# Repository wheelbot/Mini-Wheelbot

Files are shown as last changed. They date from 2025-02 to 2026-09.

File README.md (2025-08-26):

<!-- ![The Mini Wheelbot](imgs/intro.png) -->
<!-- ![Teaser](imgs/teaser.png) -->
<div align="center">
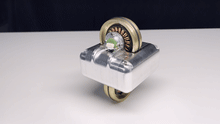
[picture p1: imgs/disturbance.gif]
  
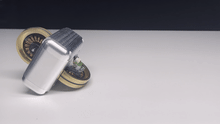
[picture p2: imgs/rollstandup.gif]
  
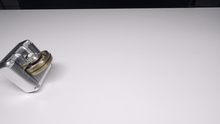
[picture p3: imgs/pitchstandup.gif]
  
</div>

<div align="center">
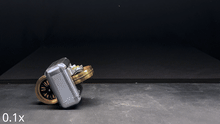
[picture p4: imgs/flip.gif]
  
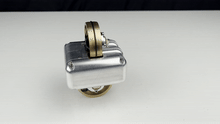
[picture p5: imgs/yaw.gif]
  
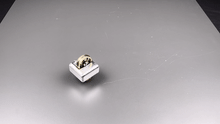
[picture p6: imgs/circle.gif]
  
</div>

# The Mini Wheelbot

The Mini Wheelbot is a **balancing, reaction wheel
unicycle robot** designed as a testbed for learning-based control.
It is an unstable system with highly nonlinear yaw dynamics, non-holonomic driving, and discrete contact switches in a small, powerful, and rugged form factor. 
The Mini Wheelbot can use its wheels to stand up from any initial orientation – enabling automatic environment resets in repetitive experiments.

## Videos
An overview of Wheelbot Hardware is available here:
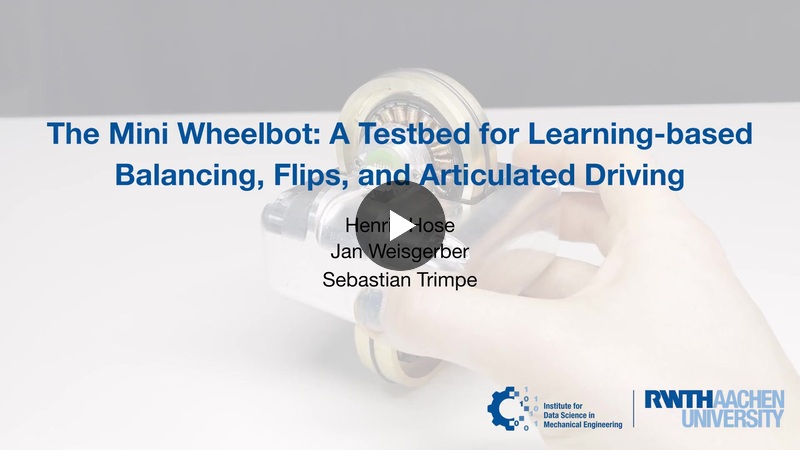
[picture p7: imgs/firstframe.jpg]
ICRA 2025 Video (https://youtu.be/_d7AqTRjz6g)


## Citation
The Mini Wheelbot is introduced in the paper:
[Henrik Hose, Jan Weisgerber, and Sebastian Trimpe. **"The Mini Wheelbot: A Testbed for Learning-based Balancing, Flips, and Articulated Driving"**, accepted to the IEEE International Conference on Robotics and Automation ICRA (2025).](http://arxiv.org/abs/2502.04582)

Please cite our paper on the Mini Wheelbot:
```bibtex
@inproceedings{hose2025miniwheelbot,
    title={The Mini Wheelbot: A Testbed for Learning-based Balancing, Flips, and Articulated Driving},
    author={Hose, Henrik and Weisgerber, Jan and Trimpe},
    year={2025},
    booktitle={2025 IEEE International Conference on Robotics and Automation (ICRA)}
}
```

## Papers using the Mini Wheelbot Hardware
The following papers use Mini Wheelbot:
- [Henrik Hose, Jan Weisgerber, and Sebastian Trimpe. **"The Mini Wheelbot: A Testbed for Learning-based Balancing, Flips, and Articulated Driving"**, accepted to the IEEE International Conference on Robotics and Automation ICRA (2025).](http://arxiv.org/abs/2502.04582)
- [Hose, Henrik, Paul Brunzema, Alexander von Rohr, Alexander Gräfe, Angela P. Schoellig, and Sebastian Trimpe. **"Fine-Tuning of Neural Network Approximate MPC without Retraining via Bayesian Optimization."** In CoRL Workshop on Safe and Robust Robot Learning for Operation in the Real World. 2024.](https://openreview.net/pdf?id=lSah6an1Ar)

## Structure of this Repo
This repo contains the following materials:
- [**PCB Schematics**](./hardware/electronics/schematic/): PCBs used on the Mini Wheelbot
- [**Meshes**](./hardware/meshes/): for visualization
- [**Wheelbot-Lib**](./wheelbot-lib/): C++20 code running on the Mini Wheelbots Buildroot Linux
- [**Scripts**](./wheelbot-lib/scripts/): Collection of Python Scripts used for system identification, keyboard control, etc.
- [**Simulation**](./simulation/): ODEs describing the Mini Wheelbot's dynamics in different Python and simulation in Acados.
- [**Microcontroller software**](./hardware/microcontroller-software/) running on STM32 microcontrollers on the Mini Wheelbot.

## Related Repos and Acknowledgements
Related repositories:
- [**Yaw control neural network approximate MPC**](https://github.com/hshose/mini-wheelbot-ampc): Dataset synthesis and neural network training in Jax for nonlinear yaw control on the Mini Wheelbot.

The Mini Wheelbot's development has been made possible thanks to these open-source projects:
- [**modm**](https://modm.io/): A modern C++ barebone embedded library generator
- [**KiCAD**](https://www.kicad.org/): A Cross Platform and Open Source Electronics Design Automation Suite
- [**CasADi**](https://web.casadi.org/): A symbolic framework for numeric optimization implementing automatic differentiation
- [**Buildroot**](https://buildroot.org/): A tool to generate embedded Linux systems through cross-compilation.
- [**acados**](https://github.com/acados/acados): Fast and embedded solvers for nonlinear optimal control.
- [**µMotor**](https://github.com/roboterclubaachen/micro-motor): A motor controller for BLDC and DC motors up to 250W.
- [**JAX**](https://jax.readthedocs.io.): Composable transformations of Python+NumPy programs.

## Contact
If you are interested in building your own Mini Wheelbot, [contact us](https://www.dsme.rwth-aachen.de/cms/dsme/das-institut/team/~ujxgg/henrik-hose/?lidx=1).

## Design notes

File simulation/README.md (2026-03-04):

# Intro
The "joints" of the wheelbot are in order:

1. The yaw angle $\psi$; its derivative is the yaw rate~$\dot{\psi}$.
2. The roll angle $\phi$; its derivative is the roll rate~$\dot{\phi}$.
3. The pitch angle $\theta$; its derivative is the pitch rate~$\dot{\phi}$.
4. The driving wheel angle $q_w$ that is actually doesn't appear in the equations of motions; its derivative is the wheel rotational velocity $\dot{q}_W$; the input torque applied to this joint is $\tau_W$.
5. The reaction wheel angle $q_w$ that is actually doesn't appear in the equations of motions; its derivative is the wheel rotational velocity $\dot{q}_R$; the input torque applied to this joint is $\tau_R$.

The generalized coordinates are: $q=[\psi,\phi,\theta,q_W, q_R]^\top$

The inputs of the wheelbot are: $u=[\tau_W, \tau_R]$

## Continuous time
In continuous time, the dynamics are of the form: $M(q)\ddot{q}+b(q,\dot{q})+g(q,u)=0$.
The mass matrix $M$, coriolis and centripedal terms $b$, and gravitational terms and inputs $g$ are also parametric in the mass and inertia of the wheels W and R, and the body of the robot, and in the wheel radius and distance from wheel rotational axis to body center of mass (assumed to be in the center of the body).

In this repository, you will find functions `fM`,`fb`,`fg` for a generic Wheelbot type of robot alongside specific `fM_WheelbotvXX`, `fb_WheelbotvXX`,`fg_WheelbotvXX` functions, where the mass and inertia parameters of the specific hardware versions are already substituted in.

# Python example
Inside the `python` folder, you find a python package with the dynamics and parameters for the new Mini Wheelbot alongside an acados simulation example.

## Installation
Install acados following the official installation instructions [here](https://docs.acados.org/installation/index.html#linux-mac).
You might need to append acados to your path, you can conveniently do this in your `.bashrc` or manually, whenever you need acados:
```
export LD_LIBRARY_PATH=$LD_LIBRARY_PATH:"/path/to/acados/lib"
export ACADOS_SOURCE_DIR="/path/to/acados"
```

I recommend to proceed with a python virtual environment from here:
```
python -m venv wheelbot-venv
source wheelbot-venv/bin/activate
```

Now install the Python interface for acados by calling:
```
pip install -e /path/to/acados/interfaces/acados_template
```
This should automatically also install casadi.
Now, you are ready to install the `wheelbot-dynamics` package as:
```
pip install -e /path/to/wheelbot-dynamics-functions/python
```

## Running the example
To run the example, you can
```
cd /path/to/wheelbot-dynamics-functions/python/wheelbot-dynamics/examples
python wheelbot_example.py
```
You should see a plot with all states of the wheelbot.

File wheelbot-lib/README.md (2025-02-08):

# Build and export dockerfile w/ cross compile
```bash
docker buildx create --use
docker buildx build --platform=linux/arm64 -t wheelbot-lib:latest --load .
docker save -o ../wheelbot-lib.container.tar wheelbot-lib:latest
```

Now, build the Buildroot image which copies over the container.
Container should be imported and started automatically upon first boot.

# Manual setup of container on the Mini Wheelbot
Contents of this repo should be at located at `/root/wheelbot-lib` on the Mini Wheelbot Pi CM4.
Run
```bash
docker compose up --build -d
```
to start the development docker container.
This will mount `./` (this repo) into the container at `/wheelbot-lib`.
The container has an ssh server at port `2233` and mounts all devices.

The docker compose file specifies restart to `always`, the container should therefore automatically start upon reboot, so you only need to do this once.

# Mounting remote `wheelbot-lib` folder on your laptop
From your laptop, you can mount the the `/root/wheelbot-lib` directory using:
```bash
sshfs -o port=22 root@192.168.0.213:/root/wheelbot-lib ~/mnt/wheelbot-lib
```

Now, you can use the IDE of your choice on your machine to develop on the Mini Wheelbot.

# Access the container for building
To compile and run the application inside the docker container
```bash
ssh -p 2233 root@192.168.0.213
```

# Building and running the Mini Wheelbot application
In a shell on the docker on the Mini Wheelbot (aka `port 2233`), go to build directory with
```
cd /wheelbot-lib/build
```
and build the software with
```
make -j8
```

In case you changed the `CMakeLists.txt`, you want to run
```
cmake ..
make -j8
```

To run the application
```
./Main
```

After you ran the application, you can find log files inside the folder
```
wheelbot-lib/log
```

# Running the Mini Wheelbot software: keyboard yaw control
In a shell on the docker on the Mini Wheelbot (aka `port 2233`), go to the `/wheelbot-lib/build` folder.
Make sure, that you are on the `jsonsetpoint` branch (should be the case for `wheelbot-beta-3`).
Now you can start the Mini Wheelbot application by:
```
./Main
```
Balance the robot on it's wheel until it stands.

On your laptop, in this repo, go to the `scripts/keyboardcontrol` folder.
You can run the keyboard input program by:
```
python main.py
```
Now you can use the `A`, `W`, `S`, and `D` keys to drive the robot around.

When closing the application, first shut down the Python window on your laptop, then close the main application on the Mini Wheelbot.

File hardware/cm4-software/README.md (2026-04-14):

# Cloning and first build
Clone the repo:
```
git clone --recursive git@git.rwth-aachen.de:dsme-projects/wheelbot/wheelbot-buildroot.git
cd wheelbot-buildroot/buildroot
```

Configure buildroot
```
make defconfig BR2_DEFCONFIG=../wheelbot_tree/configs/wheelbot_cm4_defconfig
```

Now you can build for the first time. This usually takes about 20-60min:
```
make BR2_EXTERNAL=/path/to/wheelbot-buildroot/wheelbot_tree
```

After first build, next builds are faster!

# Flashing the eMMC on the CM4
Put the CM4 on the official IO board. On J2, fit the jumper to disable eMMC boot.

You'll need [rpiboot](https://github.com/raspberrypi/usbboot) to mount the eMMC. First, call
```
rpiboot
```

Then power on the CM4. You should see output like:
```
$ rpiboot
RPIBOOT: build-date Jul 10 2023 version 20221215~105525 c4b12f85
Waiting for BCM2835/6/7/2711...
Loading embedded: bootcode4.bin
Sending bootcode.bin
Successful read 4 bytes
Waiting for BCM2835/6/7/2711...
Loading embedded: bootcode4.bin
Second stage boot server
Cannot open file config.txt
Cannot open file pieeprom.sig
Loading embedded: start4.elf
File read: start4.elf
Cannot open file fixup4.dat
Second stage boot server done
```

And with `lsblk`, a disk called `sdX` should appear.

Now you can use the copying tool of your trust, e.g., `dd` (beware, `dd` is dangerous):
```
cd output/images
dd if=sdcard.img of=/dev/sdX bs=64k status=progress && sync
```

# Accessing the Pi
While still on IO board, you can hook up monitor, mouse and keyboar.

Once you place the CM4 on the wheelbot compute carrier, you can only access over WIFI, i.e. the `botnet` Wifi via `ssh`:
```
ssh root@192.168.10.XXX
```

# Notes

```
rm -rf output/build/linux-* && rm -rf output/target/root/wheelbot-ros && make defconfig BR2_DEFCONFIG=../wheelbot_tree/configs/wheelbot_cm4_defconfig && make BR2_EXTERNAL=/home/hose/projects/dsme/wheelbot-buildroot/wheelbot_tree

rm -rf output/build/linux-* && rm -rf output/target/root/wheelbot-ros && make defconfig BR2_DEFCONFIG=../wheelbot_tree/configs/wheelbot_cm4_defconfig && make linux-menuconfig CONFIG_EXPERT=y
```

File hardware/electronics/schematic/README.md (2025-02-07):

## Schematics for PCBs in the Wheelbot

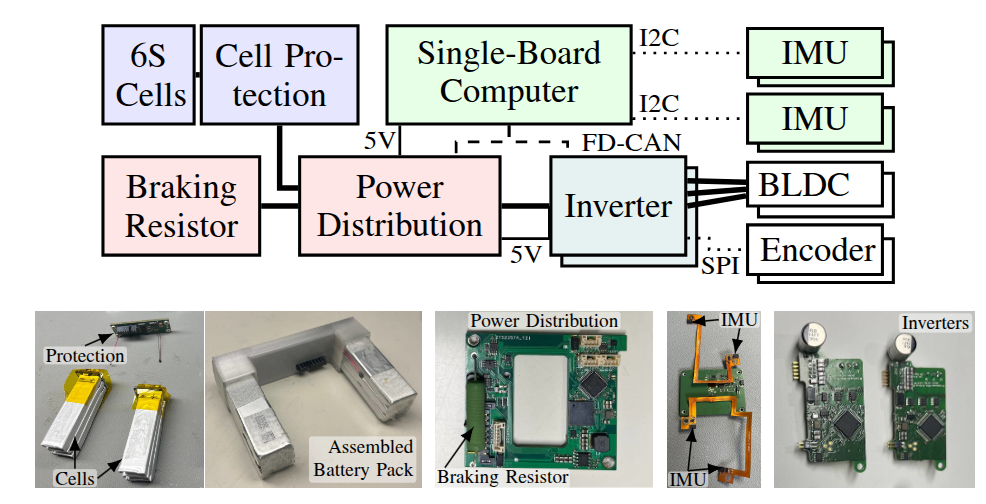
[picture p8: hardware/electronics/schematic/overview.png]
electronics overview


For details on the micro-motor, please visit the [https://github.com/roboterclubaachen/micro-motor](https://github.com/roboterclubaachen/micro-motor)

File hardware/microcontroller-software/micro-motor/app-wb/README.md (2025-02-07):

# Installation of toolchain
follow the [instructions for modm installation, including the ARM Cortex-M toolchain](https://modm.io/guide/installation/)

# Compile the firmware
You can compile the firmware with
```
scons -j8
```

And you can program the motorcontroller with:
```
scons program
```

# Changes from modm
MODM generated files are committed directly, if you want to update the generated files, call `lbuild build` and you should see the required files.

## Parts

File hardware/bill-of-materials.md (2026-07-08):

# Bill of Materials
** This list is work in progress and not yet complete ** 

## CNC Parts
| Item | Description | Qty | Vendor |
| ---- | ---- | --- | --- |
| [Frame](mechanical/step/frame.stp) | ISO 2768 medium, material aluminium 6061 or 6081, 8x M3 and 4x M2.5 Threads | 1 | [https://xometry.eu](https://xometry.eu) |
| [Wheel](mechanical/step/reactionwheel.stp) |  ISO 2768 fine, material brass MS58, one surface to H5 tolerance | 2 | [https://xometry.eu](https://xometry.eu) |
| [Lid](mechanical/step/lid.stp) | ISO 2768 medium, material aluminium 6061 or 6081 | 2 | [https://xometry.eu](https://xometry.eu) |

## Motors
| Item | Description | Qty | Vendor |
| ---- | ---- | --- | --- |
| Motors | T-Motor MN4006 KV380 (see note below) | 2 (sold as 1 set) | [T-Motor](https://store.tmotor.com/product/mn4006-kv380-motor-antigravity-type.html) |
| Encoder magnet | N35SH D=6mm t=2.5mm | 2 | [DigiKey](https://www.digikey.de/de/products/detail/radial-magnets-inc/9049/6030786) | 
| O-Ring | 56mm x 2mm NBR90 | 2 (get some spare!) | Maybe [McMaster](https://www.mcmaster.com/1247N172/) |

**Note on the motors**: There is a new [T-Motor MN4006 KV380 **EVO**](https://store.tmotor.com/de/product/mn4006-EVO-kv380-motor-antigravity-type.html) version of the motor with 150C temperature rated magnets, which I highly recommend using in new builds, however the tolerances in the flywheel are slightly different. The existing flywheel inner diameter is too large, which can only partially compensated by epoxy.

## Custom PCBs
| Item | Description | Qty | Vendor |
| ---- | ---- | --- | --- |
| Power Distribution [schematics](electronics/schematic/power-distribution.pdf), [gerbers](electronics/gerbers/power-distribution/power-distribution-v1.kicad_pcb_gerber.zip) | 4 layer, 1.6mm, 5/5 mil spacing, 0.2mm min hole | 1 | [http://pcbway.com/](http://pcbway.com/) |
| Motor Controller [schematics](electronics/schematic/micro-motor.pdf), [gerbers](electronics/gerbers/micro-motor-wb/micro-motor-v2.2WB.kicad_pcb_gerber.zip) | 4 layer, 1.6mm, 5/5 mil spacing, 0.2mm min hole | 2 | [http://pcbway.com/](http://pcbway.com/) |
| Flex PCB IMU 1 [schematics](electronics/schematic/imu-flex.pdf), [gerbers](electronics/gerbers/imu-flex-1/imu-flex-1-v1.kicad_pcb_gerber.zip) | 2 layer, 0.1mm, [FR4 Stiffener on frontside](electronics/gerbers/imu-flex-1/imu-flex-1-v1-stiffener_on_front.png), [max. dimensions 52x73.5mm](electronics/gerbers/imu-flex-1/imu-flex-1-v1-dimensions.png) | 1 | [http://pcbway.com/](http://pcbway.com/) | 
| Flex PCB IMU 2 [schematics](electronics/schematic/imu-flex.pdf), [gerbers](electronics/gerbers/imu-flex-2/imu-flex-2-v1.kicad_pcb_gerber.zip) | 2 layer, 0.1mm, [FR4 Stiffener on backside](electronics/gerbers/imu-flex-2/imu-flex-2-v1-stiffener_on_back.png), [max. dimensions 59x67.158mm](electronics/gerbers/imu-flex-2/imu-flex-2-v1-dimensions.png) | 1 | [http://pcbway.com/](http://pcbway.com/) |
| Compute Carrier [schematics](electronics/schematic/compute-carrier.pdf), [gerbers](electronics/gerbers/computecarrier/computecarrier-v1.kicad_pcb_gerber.zip) | 2 layer, 1.6mm | 1 | [http://pcbway.com/](http://pcbway.com/) |
| Cell Protection [schematics](electronics/schematic/cell-protection.pdf), [gerbers](electronics/gerbers/cell-protection/cell-protection-v1.kicad_pcb_gerber.zip) | 2 layer, 1.6mm | 1 | [http://pcbway.com/](http://pcbway.com/) |
| Cell Adapter [gerbers](electronics/gerbers/cell-adapter/cell-adapter-v1.kicad_pcb_gerber.zip) | 2 layer, 1.6mm, 2x press fit holes! | 2 | [http://pcbway.com/](http://pcbway.com/) |
| 3-phase cable extension [gerbers](electronics/gerbers/motorcon/motorcon-v1.kicad_pcb_gerber.zip) | 2 layer, 1.6mm | 1 | [http://pcbway.com/](http://pcbway.com/) |
| Encoder [schematics](electronics/schematic/encoder.pdf), [gerbers](electronics/gerbers/encoder/encoder-v1.kicad_pcb_gerber.zip) | 2 layer, 1.6mm | 2 | [http://pcbway.com/](http://pcbway.com/) | 
| Charger [schematics](electronics/schematic/charger.pdf), [gerbers](electronics/gerbers/charger/ui-v2.kicad_pcb_gerber.zip) |4 layer, 1.6 mm | 1 | [http://pcbway.com/](http://pcbway.com/) | 

## Battery Pack
| Item | Description | Qty | Vendor |
| ---- | ---- | --- | --- |
| LiPo battery cells | Tattu 450mAH 75C XT30 Long 61x16mm cells from 2S,3S or 4S packs, e.g., TA-75C-450-2S1P-L | 6 cells (e.g., from 3 2S packs) | [fpv24.com](https://www.fpv24.com/de/tattu/tattu-batterie-lipo-akku-2s-450-mah-30c-xt30-lang) |
| Shrink wrap | 36mm wide when flat LiPO battery shrink wrap | <0.30m per robot | [Aliexpress](https://www.aliexpress.com/item/1005001749492020.html) |
| 3M ET 1339 tape | fiber reinforced polyester film tape, 15mm wide (can be more) | <1m per robot | [DigiKey](https://www.digikey.com/en/products/detail/3m-tc/1339-1-60/7571874) |
| Electrical grade silicone | Chip Quik EGS10C­20G | 1 | [DigiKey](https://www.digikey.com/en/products/detail/chip-quik-inc/EGS10C-20G/10059587) |
| Isolated NTC 10k | NRMR104F3435B2F NTC 10k B 3435K isolated leads | 2 | [DigiKey](https://www.digikey.com/en/products/detail/eaton-electronics-division/NRMR104F3435B2F/15927881) |

## Bolts and Fasteners
| Item | Description | Qty | Vendor |
| ---- | ---- | --- | --- |
| M2.5 nuts flat | DIN 439 M2.5 hex nut flat stainless A1/A2 | 8 | [McMaster](https://www.mcmaster.com/90710A025/) |
| M2.5x10mm set screw | DIN 913 set screw stainless A1/A2 M2.5x10 | 4 | [McMaster](https://www.mcmaster.com/92605A073/) |
| M2x6mm flat head screw | DIN 965 flat head torx stainless A1/A1 M2x6mm | 2 | [McMaster](https://www.mcmaster.com/92703A145/) |
| M2.5x6mm flat head screw | DIN 965 flat head torx stainless A1/A2 M2.5x6mm | 2 | [McMaster](https://www.mcmaster.com/92703A158/) |
| M3x20mm flat head screw | DIN 965 flat head torx stainless A1/A2 M3x20mm | 2 | [McMaster](https://www.mcmaster.com/92703A455/) |
| M2x4mm socket head screw | DIN912 socket head hex stainless A1/A2 M2x4mm | 6 | [McMaster](https://www.mcmaster.com/91292A004/) |
| M2x8mm socket head screw | DIN912 socket head hex stainless A1/A2 M2x8mm | 1 | [McMaster](https://www.mcmaster.com/91292A832/) |
| M2.5x4mm socket head screw | DIN912 socket head hex stainless A1/A2 M2.5x4mm | 5 | [McMaster](https://www.mcmaster.com/91292A015/) |
| M3x6mm socket head screw | DIN912 socket head hex stainless A1/A2 M3x6mm | 14 | [McMaster](https://www.mcmaster.com/91292A112/) |
| M3x8mm socket head screw | DIN912 socket head hex stainless A1/A2 M3x8mm | 2 | [McMaster](https://www.mcmaster.com/91292A111/) |
| M2x3mm threaded 3D print insert | Brass heat-set inserts for plastic, M2x3mm | 2 | [McMaster](https://www.mcmaster.com/94459A110/) | 
| M2.5x4mm threaded 3D print insert | Brass heat-set inserts for plastic, M2.5x4mm | 7 | [McMaster](https://www.mcmaster.com/94459A768/) | 
| M2 washer | DIN125 stainless steel general purpose washer M2 | 4 | [McMaster](https://www.mcmaster.com/93475A195/) |

# Precrimped Cables and Connector Housings
| Item | Description | Qty | Vendor |
| ---- | ---- | --- | --- |
| JST-GH 2in | AGHGH28K51 precrimped 2in 28AWG single wire | 12 | [DigiKey](https://www.digikey.de/de/products/detail/jst-sales-america-inc/AGHGH28K51/6009448) |
| JST-GH 6in | AGHGH28K152 precrimped 6in 28AWG single wire | 6 | [DigiKey](https://www.digikey.de/de/products/detail/jst-sales-america-inc/AGHGH28K152/6009449) |
| JST-XH 2in | ASXHSXH22K51 precrimped 2in 22AWG single wire | 6 | [DigiKey](https://www.digikey.de/de/products/detail/jst-sales-america-inc/ASXHSXH22K51/6684930) |
| JST-XH 4in | ASXHSXH22K102 precrimped 4in 22AWG single wire | 3 | [DigiKey](https://www.digikey.de/de/products/detail/jst-sales-america-inc/ASXHSXH22K102/9961917) | 
| JST GH 6 pin plug housing | GHR-06V-S | 6 | [DigiKey](https://www.digikey.de/de/products/detail/jst-sales-america-inc/GHR-06V-S/807818) |
| JST XH 3 pin plug housing | XHP-3 | 3 | [DigiKey](https://www.digikey.de/de/products/detail/jst-sales-america-inc/XHP-3/1651017) |

## MISC
| Item | Description | Qty | Vendor |
| ---- | ---- | --- | --- |
| Quick set epoxy | Any 5 min Epoxy | a few drops | [McMaster](https://www.mcmaster.com/7541A76/) |
| Shielding copper tape | 3M Copper Tape | a small strip | [DigiKey](https://www.digikey.de/de/products/detail/3m-tc/3M-9876-15-12-X-12-SHEET/9841909) |
| Raspberry Pi CM4 | at least 8GB RAM, 16GB EMMC, with WIFI | 1 | [DigiKey](https://www.digikey.de/en/products/detail/raspberry-pi/SC0677/13530927) |
| Heat shrink | 3:1 heat shrink with glue for 22AWG single wires, 30-40mm length | 9 | |

## 3D Prints
| Item | Description | Qty | Vendor |
| ---- | ---- | --- | --- |
| [Battery housing](mechanical/meshes/battery_front.stl) | PETG or other high-temp filament, NO PLA | 1 | |
| [Battery lid](mechanical/meshes/battery_back.stl) | PETG or other high-temp filament, NO PLA | 1 | |
| [Internal frame 1](mechanical/step/electronics_frame_split_1.stp), can be printed in two pieces [a](mechanical/meshes/electronics_frame_split_1-a.stl) and [b](mechanical/meshes/electronics_frame_split_1-b.stl) and glued | PETG or other high-temp filament, NO PLA | 1 | |
| [Internal frame 2](mechanical/step/electronics_frame_split_2.stp), can be printed in two pieces [a](mechanical/meshes/electronics_frame_split_2-a.stl) and [b](mechanical/meshes/electronics_frame_split_2-b.stl) and glued | PETG or other high-temp filament, NO PLA | 1 | |
| [Magnet holder](mechanical/meshes/magnet_adapter.stl) | PETG or other high-temp filament, NO PLA | 1 | |

## Tools
| Item | Description | Qty | Vendor |
| ---- | ---- | --- | --- |
| ST-Link V2 Programmer | SWD Programmer | 1 | [Amazon](https://amzn.eu/d/00pj816s) |
| TTL to USB Adapter | UART Debugger | 1 | [Amazon](https://amzn.eu/d/01Bp48ve) |
| CAN Adapter | CAN USB-Interface | 1 | [Amazon](https://amzn.eu/d/08WZT5C6) |
| CAN Pin Terminal | CAN Pin Terminal Female | 1 | [Amazon](https://amzn.eu/d/05fRgW5H) |
| JST-GH 6in | AGHGH28K152 precrimped 6in 28AWG single wire | 9 | [DigiKey](https://www.digikey.de/de/products/detail/jst-sales-america-inc/AGHGH28K152/6009449) |
| JST GH 3 pin plug housing | GHR-03V-S | 3 | [DigiKey](https://www.digikey.de/de/products/detail/jst-sales-america-inc/GHR-03V-S/807815) |
| Syringe | 10ml disposable syringes with wide-lumen needle for applying epoxy | 1+ | |

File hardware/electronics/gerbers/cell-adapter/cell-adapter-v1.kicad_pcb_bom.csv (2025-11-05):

DESIGNATOR | QTY | MANUFACTURER | VALUE | FOOTPRINT | MPN | DESCRIPTION | MOUNT TYPE
H3, H4 | 2 | Mill-Max | 0531-0-15-15-31-27-10-0 | 0531-0-15-15-31-27-10-0 | 0531-0-15-15-31-27-10-0 | PRESS FIT INSERT, HEX AT FRONT LAYER (marked “SOLDER ON THIS SIDE”) | tht

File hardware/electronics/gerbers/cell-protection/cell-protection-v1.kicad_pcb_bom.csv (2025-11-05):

DESIGNATOR | QTY | MANUFACTURER | VALUE | FOOTPRINT | MPN | DESCRIPTION | MOUNT TYPE
C1, C12, C13, C14, C15, C2, C3, C4, C5, C6, C7, C9 | 12 |  | 1u | C_0402_1005Metric |  | MLCC 0402 50V X7S/R | smt
C10 | 1 |  | DNP | C_0402_1005Metric |  |  | smt
C11 | 1 |  | DNP | C_0402_1005Metric |  |  | smt
C8 | 1 |  | DNP | C_0402_1005Metric |  |  | smt
D1, D5 | 2 | NXP | BAS16J,135 | D_SOD-323F | BAS16J,135 | DIODE | smt
D2, D3 | 2 | NEXPERIA | PDZ16B,115 | D_SOD-323 | PDZ16B,115 | ZENER DIODE | smt
D4 | 1 |  | SMF24CA | D_SOD-123F | SMF24CA | TVS DIODE | smt
J1 | 1 | TE CONNECTIVITY | 1827685-1 or 1827685-4 | 1827685-1 | 1827685-1 or 1827685-4 | CONNECTOR, alternative: 1827685-4 | tht
J2, J3, J4, J5 | 4 | Mill-Max | 9137-0-00-15-00-00-38-0 | 9137-0-00-15-00-00-38-0 | 9137-0-00-15-00-00-38-0 | SPECIAL MOUNTING INSTRUCTIONS!!! NAIL PIN | tht
R1, R23, R6 | 3 |  | 1k | R_0402_1005Metric |  | RESISTOR 1% 0402 | smt
R10, R2, R3, R4, R5, R7, R8, R9 | 8 |  | 33R | R_0402_1005Metric |  | RESISTOR 1% 0402 | smt
R11, R13 | 2 |  | 100R | R_0402_1005Metric |  | RESISTOR 1% 0402 | smt
R12 | 1 | BOURNS | CSS2H-2512K-3L00F | R_2512_6332Metric | CSS2H-2512K-3L00F | SHUNT 3mOhm 4W | smt
R14 | 1 |  | 4k5 | R_0402_1005Metric |  | RESISTOR 1% 0402 | smt
R15, R31 | 2 |  | 1M | R_0402_1005Metric |  | RESISTOR 1% 0402 | smt
R16, R22 | 2 |  | 10M | R_0402_1005Metric |  | RESISTOR 1% 0402 | smt
R17, R19, R21, R25, R29, R30 | 6 |  | 10k | R_0402_1005Metric |  | RESISTOR 1% 0402 | smt
R18, R20 | 2 |  | 750k | R_0402_1005Metric |  | RESISTOR 1% 0402 | smt
R24 | 1 |  | 3M3 | R_0402_1005Metric |  | RESISTOR 1% 0402 | smt
R26, R27, R28 | 3 |  | 450k | R_0402_1005Metric |  | RESISTOR 1% 0402 | smt
U1, U4 | 2 | VISHAY | SIR180ADP-T1-RE3 | PowerPAK_SO-8_Single | SIR180ADP-T1-RE3 | NFET 60V 137A | smt
U2, U3 | 2 | TEXAS INSTRUMENTS | BQ7791508PW | TSSOP-24_4.4x7.8mm_P0.65mm | BQ7791508PW | BATTERY PROTECTION IC | smt

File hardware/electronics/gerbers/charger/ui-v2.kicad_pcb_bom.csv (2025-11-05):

DESIGNATOR | QTY | MANUFACTURER | VALUE | FOOTPRINT | MPN | DESCRIPTION | MOUNT TYPE
C1 | 1 |  | 33n | C_0402_1005Metric |  | MLCC 0402 50V X7S/R | smt
C10, C11, C18 | 3 |  | 10u 6.3V | C_0603_1608Metric |  | MLCC 0603 50V X7S/R | smt
C12, C13, C9 | 3 |  | 100n | C_0402_1005Metric |  | MLCC 0402 50V X7S/R | smt
C14, C15 | 2 |  | 330p | C_0402_1005Metric |  | MLCC 0402 50V X7S/R | smt
C16, C2, C4, C7 | 4 |  | 10u 50V | C_1206_3216Metric |  | MLCC 1206 50V X7S/R | smt
C17, C3, C5, C8 | 4 |  | 1u 50V | C_0603_1608Metric |  | MLCC 0603 50V X7S/R | smt
C6 | 1 |  | 4.7nF | C_0402_1005Metric |  | MLCC 0402 50V X7S/R | smt
D1 | 1 |  | LED_RED | LED_0402_1005Metric_Pad0.77x0.64mm_HandSolder |  | LED RED 0402 | smt
D3 | 1 | DIODES INC | B140-13-F | D_SMA | B140-13-F | SCHOTTKY 40V 1A SMA | smt
H1, H2 | 2 | WUERTH | 9774040243 | Mounting_Wuerth_WA-SMSI-M2_H4mm_9774040243 | 9774040243 | WUERT STANDOFF M2 H4 SMSI | smt
J1 | 1 | JST | SM06B-GHS-TBT | JST_GH_SM06B-GHS-TB_1x06-1MP_P1.25mm_Horizontal | SM06B-GHS-TBT | CON 6 POL | smt
J2 | 1 | GCT | USB4140-GF-0170-C | GCT_USB4140-GF-0170-C_REV0.4 | USB4140-GF-0170-C | USB C CON | smt
L1 | 1 | COILCRAFT | XGL5030-103MEC | L_Coilcraft_XAL5030-XXX | XGL5030-103MEC | INDUCTOR 10uH 5.7A | smt
R1 | 1 |  | 194k | R_0402_1005Metric |  | RESISTOR 1% 0402 | smt
R10, R2 | 2 |  | 10k | R_0402_1005Metric |  | RESISTOR 1% 0402 | smt
R4 | 1 |  | 40.2k | R_0402_1005Metric |  | RESISTOR 1% 0402 | smt
R11, R12, R17, R18, R20, R24, R7, R8, R9 | 9 |  | 100k | R_0402_1005Metric |  | RESISTOR 1% 0402 | smt
R13, R15 | 2 |  | 12k1 | R_0402_1005Metric |  | RESISTOR 1% 0402 | smt
R14 | 1 |  | 115k | R_0402_1005Metric |  | RESISTOR 1% 0402 | smt
R16 | 1 |  | 5k1 | R_0402_1005Metric |  | RESISTOR 1% 0402 | smt
R3 | 1 | THIN FILM TECH CORP | D1WEL1206MR200D-T5 | R_1206_3216Metric | D1WEL1206MR200D-T5 | RES 0.2 OHM 1206 | smt
R5 | 1 |  | 1k | R_0402_1005Metric |  | RESISTOR 1% 0402 | smt
R6 | 1 |  | 352k | R_0402_1005Metric |  | RESISTOR 1% 0402 | smt
SW1 | 1 | C&K | JS202011CQN | SW_CK_JS202011CQN_DPDT_Straight | JS202011CQN | SWITCH DPDT | tht
U1 | 1 | ANALOG DEVICES | LT3477EUF#PBF | QFN-20-1EP_4x4mm_P0.5mm_EP2.5x2.5mm | LT3477EUF#PBF | BOOST CV CC | smt
U2 | 1 | TEXAS INSTRUMENTS | TPS25730DREFR | Texas_REF0038A_WQFN-38-2EP_6x4mm_P0.4 | TPS25730DREFR | USB C PD CONTROLLER | smt
U3 | 1 | TEXAS INSTRUMENTS | TVS2200DRVR | WSON-6-1EP_2x2mm_P0.65mm_EP1x1.6mm | TVS2200DRVR | TVS PROTECTION | smt

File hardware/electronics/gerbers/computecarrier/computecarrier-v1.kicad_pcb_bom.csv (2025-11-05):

DESIGNATOR | QTY | MANUFACTURER | VALUE | FOOTPRINT | MPN | DESCRIPTION | MOUNT TYPE
C1, C2, C5, C6 | 4 |  | 100n | C_0402_1005Metric |  | MLCC 0402 50V X7S/R | smt
D1 | 1 |  | SMAJ5.0 | D_SMA | SMAJ5.0 | TVS DIODE | smt
D2 | 1 |  | LED Green | LED_0402_1005Metric |  | LED 0402 GREEN | smt
D3 | 1 |  | LED Red | LED_0402_1005Metric |  | LED 0402 RED | smt
D5 | 1 | DIOTEC | NUP2105L | SOT-23 | NUP2105L | ESD DIODE | smt
H1, H2, H3, H4 | 4 |  | DNP |  |  |  | smt
J2, J8 | 2 | HIROSE | BK13C06-10DS/2-0.35V(895) | Hirose_BK13C06-10DS_2x06_P0.35mm | BK13C06-10DS/2-0.35V(895) | CON | tht
J6 | 1 | SAMTEC | FTSH-102-02-F-D-RA | PinHeader_2x02_P1.27mm_Horizontal | FTSH-102-02-F-D-RA | PIN HEADER | tht
J7 | 1 | JST | BM03B-GHS-TBT | JST_GH_BM03B-GHS-TBT_1x03-1MP_P1.25mm_Vertical |  | CON | smt
Module1 | 2 | HIROSE | 2x DF40C-100DS-0.4V | Raspberry-Pi-4-Compute-Module | DF40C-100DS-0.4V | HD CON (2x) | smt
Q1 | 1 | NEXPERIA | PMV65XP,215 | SOT-23 |  | PFET | smt
R1, R2, R3, R4, R5, R8 | 6 |  | 3k3 | R_0402_1005Metric |  | RESISTOR 1% 0402 | smt
R10 | 1 |  | 0R | R_0402_1005Metric |  | RESISTOR 1% 0402 | smt
R11, R9 | 2 |  | 1k | R_0402_1005Metric |  | RESISTOR 1% 0402 | smt
R12 | 1 |  | DNP | R_0402_1005Metric_Pad0.72x0.64mm_HandSolder |  |  | smt
R6 | 1 |  | 120R | R_0805_2012Metric_Pad1.20x1.40mm_HandSolder |  | RESISTOR 1% 0805 | smt
U1 | 1 | ONSEMI | CAT24C256HU4IGT3 | DFN-8-1EP_3x2mm_P0.5mm_EP1.3x1.5mm | CAT24C256HU4IGT3 | EEPROM | smt
U2, U3 | 2 | DIODES | 74LVC1G07SE-7 | SOT-353_SC-70-5 |  | BUFFER | smt
U6 | 1 | MICROCHIP | MCP2517FD-H/JHA | DFN-14-1EP_3x4.5mm_P0.65mm_EP1.65x4.25mm |  | CAN IC | smt
U7 | 1 | TEXAS INSTRUMENTS | TCAN330GDCNT | SOT-23-8 |  | CAN TRANSCEIVER | smt
Y2 | 1 | MURATA | CSTNE20M0V53Z000R0 | Resonator_SMD_Murata_CSTxExxV-3Pin_3.0x1.1mm |  | 20MHz CERAMIC RESONATOR | smt

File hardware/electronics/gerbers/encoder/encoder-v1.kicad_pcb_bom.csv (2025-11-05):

DESIGNATOR | QTY | MANUFACTURER | VALUE | FOOTPRINT | MPN | DESCRIPTION | MOUNT TYPE
C1, C2 | 2 |  | 1u | C_0402_1005Metric |  | MLCC 0402 50V X7S/R | smt
C3 | 1 |  | 100n | C_0402_1005Metric |  | MLCC 0402 50V X7S/R | smt
J1 | 1 | JST | SM06B-GHS-TB | JST_GH_SM06B-GHS-TB_1x06-1MP_P1.25mm_Horizontal | SM06B-GHS-TB | JST CON 6POS | smt
R1 | 1 |  | DNP | R_0402_1005Metric |  |  | smt
R10, R11, R8, R9 | 4 |  | 0R | R_0402_1005Metric |  | RESISTOR 1% 0402 | smt
R2 | 1 |  | DNP | R_0402_1005Metric |  |  | smt
R3 | 1 |  | DNP | R_0402_1005Metric |  |  | smt
R4 | 1 |  | 10k | R_0402_1005Metric |  | RESISTOR 1% 0402 | smt
R5 | 1 |  | DNP | R_0402_1005Metric |  |  | smt
R6 | 1 |  | DNP | R_0402_1005Metric |  |  | smt
R7 | 1 |  | DNP | R_0402_1005Metric |  |  | smt
U1 | 1 | AMS | AS5047D-ATSM | TSSOP-14_4.4x5mm_P0.65mm |  | ON AXIS MAGNET ROTARY ENCODER | smt

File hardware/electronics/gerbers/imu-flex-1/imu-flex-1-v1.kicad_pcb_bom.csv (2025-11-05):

DESIGNATOR | QTY | MANUFACTURER | VALUE | FOOTPRINT | MPN | DESCRIPTION | MOUNT TYPE
C1 | 1 |  | DNP | C_0402_1005Metric |  |  | smt
C10, C4, C5, C9 | 4 |  | 100n | C_0402_1005Metric |  | MLCC 0402 25V X7S/R | smt
C2, C3, C7, C8 | 4 |  | 2u2 | C_0402_1005Metric |  | MLCC 0402 25V X7S/R | smt
C6 | 1 |  | DNP | C_0402_1005Metric |  |  | smt
J1 | 1 | HIROSE | BK13C06-10DP/2-0.35V(895) | Hirose_BK13C06-10DP_2x06_P0.35mm | BK13C06-10DP/2-0.35V(895) | CON | smt
L1, L2 | 2 | TDK | MLZ1005M1R0WT000 | L_0402_1005Metric | MLZ1005M1R0WT000 | 1uH INDUCTOR | smt
R1, R5 | 2 |  | 0R | R_0402_1005Metric |  | RESISTOR 1% 0402 | smt
U1, U3 | 2 | TEXAS INSTRUMENTS | LP2980AIM5X-3.0/NOPB | SOT-23-5 |  | 3V FIXED LDO | smt
U2, U4 | 2 | BOSCH SENSORTEC | BMI088 | bmi088 | BMI088 | IMU | smt

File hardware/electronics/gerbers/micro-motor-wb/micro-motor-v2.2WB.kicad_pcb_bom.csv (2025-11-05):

DESIGNATOR | QTY | MANUFACTURER | VALUE | FOOTPRINT | MPN | DESCRIPTION | MOUNT TYPE
C1, C2, C404 | 3 |  | 1µ | C_0402_1005Metric |  | MLCC 0402 50V X7S/R | smt
C10, C11, C12, C13, C14, C15, C16, C17, C20, C21, C22, C23, C24, C25, C407, C408, C409, C7, C8, C9 | 20 |  | 10u 50V | C_1206_3216Metric |  | MLCC 1206 50V X7S/R | smt
C201, C301, C302, C303, C304, C305, C306, C402, C403, C410, C411, C412 | 12 |  | 100n | C_0402_1005Metric |  | MLCC 0402 50V X7S/R | smt
C3 | 1 |  | 100p | C_0402_1005Metric |  | MLCC 0402 50V X7S/R | smt
C307 | 1 |  | 1u | C_0402_1005Metric |  | MLCC 0402 50V X7S/R | smt
C4, C501, C503 | 3 |  | 22µ 16V | C_0805_2012Metric |  | MLCC 0805 16V X7S/R | smt
C401 | 1 | PANASONIC | EEHAZT1H680B | CP_Radial_D8.0mm_P3.50mm | EEHAZT1H680B | SPECIAL MOUNTING INSTRUCTIONS!!! Alu Poly Elec Radial 68u 50V | tht
C405 | 1 |  | 1µ 16V X7R | C_0603_1608Metric |  | MLCC 0603 16V X7R | smt
C406 | 1 |  | 47n 50V X7R | C_0402_1005Metric |  | MLCC 0402 50V X7S/R | smt
C5, C6 | 2 |  | 20p | C_0402_1005Metric |  | MLCC 0402 50V C0G | smt
D1 | 1 |  | SMAJ22A | D_SMA | SMAJ22A | TVS DIODE 400W | smt
D301 | 1 |  | LED_B | LED_0402_1005Metric |  | LED 0402 BLUE | smt
D302 | 1 |  | LED_R | LED_0402_1005Metric |  | LED 0402 RED | smt
D303 | 1 |  | LED_G | LED_0402_1005Metric |  | LED 0402 GREEN | smt
J1 | 1 | SAMTEC | FTSH-105-02-F-D-RA | PinHeader_2x05_P1.27mm_Horizontal | FTSH-105-02-F-D-RA | PIN HEADER | tht
J106 | 1 | JST | B3B-XH-A | JST_XH_B3B-XH-A_1x03_P2.50mm_Vertical | B3B-XH-A | CON 3POS | tht
J2 | 1 | JST | BM06B-GHS-TBT | JST_GH_BM06B-GHS-TBT_1x06-1MP_P1.25mm_Vertical | BM06B-GHS-TBT | CON 6POS | smt
J302, J303 | 2 | JST | BM03B-GHS-TBT | JST_GH_BM03B-GHS-TBT_1x03-1MP_P1.25mm_Vertical | BM03B-GHS-TBT | CON 3POS | smt
J6 | 1 | SAMTEC | FTSH-102-02-F-D-RA | PinHeader_2x02_P1.27mm_Horizontal | FTSH-102-02-F-D-RA | PIN HEADER | tht
Q401, Q402, Q403 | 3 | ONSEMI | FDMD8240L (alternatives: FDMD8260L or FDMD8260LET60) | DFN-12-2EP_3.3x5mm_Pitch0.65mm | FDMD8240L | DUAL NMOS 40V, 98A | tht
R1 | 1 |  | 22k1 | R_0402_1005Metric |  | RESISTOR 1% 0402 | smt
R102, R104, R106, R109 | 4 |  | 20k | R_0402_1005Metric |  | RESISTOR 1% 0402 | smt
R103, R105, R107, R110, R304, R305, R306 | 7 |  | 1k | R_0402_1005Metric |  | RESISTOR 1% 0402 | smt
R114 | 1 |  | 0R | R_0402_1005Metric |  | RESISTOR 1% 0402 | smt
R2, R401 | 2 |  | 10k | R_0402_1005Metric |  | RESISTOR 1% 0402 | smt
R402, R403, R404 | 3 | KOA SPEER | TLR2ATTD3L00F | R_0805_2012Metric | TLR2ATTD3L00F | SHUNT 3mOHM 1% 1W | smt
TH1 | 1 | PANASONIC | ERT-J0EG103FA | R_0402_1005Metric | ERT-J0EG103FA | NTC 10k 0402 1% | smt
U1 | 1 | TEXAS INSTRUMENTS | LP2980AIM5X-3.0/NOPB | SOT-23-5 | LP2980AIM5X-3.0/NOPB | 3.0V FIXED LDO | smt
U2, U3, U4 | 3 | TEXAS INSTRUMENTS | INA241A2IDDFR | SOT-23-8 | INA241A2IDDFR | CURRENT SENSE AMP | smt
U201 | 1 | TEXAS INSTRUMENTS | TCAN330GDCNT | SOT-23-8 | TCAN330GDCNT | 3.3V CAN TRANSCEIVER | smt
U301 | 1 | ST MICROELECTRONICS | STM32G474CET6 | LQFP-48_7x7mm_P0.5mm | STM32G474CET6 | MICROCONTROLLER | smt
U401 | 1 | TEXAS INSTRUMENTS | DRV8320SRTVT | QFN-32-1EP_5x5mm_P0.5mm_EP3.45x3.45mm | DRV8320SRTVT | 3-PHASE SMART GATE DRIVER | smt
U501 | 1 | CYNTEC | MUN12AD01-SH | Converter_DCDC_Cyntec_MUN12AD01-SH | MUN12AD01-SH | DC-DC Module 1V-5V 1A | smt
Y1 | 1 | ABRACOM | ASCO-24.000MHZ-EK-T3 | Oscillator_SMD_Abracon_ASCO-4Pin_1.6x1.2mm | ASCO-24.000MHZ-EK-T3 | OSCILLATOR | smt

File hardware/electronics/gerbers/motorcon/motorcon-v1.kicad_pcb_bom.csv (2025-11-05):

DESIGNATOR | QTY | MANUFACTURER | VALUE | FOOTPRINT | MPN | DESCRIPTION | MOUNT TYPE
J2 | 1 | JST | B3B-XH-A(LF)(SN) | JST_XH_B3B-XH-A_1x03_P2.50mm_Vertical | B3B-XH-A(LF)(SN) | JST CON HEADER | tht

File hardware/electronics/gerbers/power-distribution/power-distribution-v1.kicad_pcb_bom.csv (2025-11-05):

DESIGNATOR | QTY | MANUFACTURER | VALUE | FOOTPRINT | PACKAGE | MPN | DESCRIPTION | MOUNT TYPE
BZ1 | 1 | MURATA | PKMCS0909E4000-R1 | Buzzer_CUI_CPT-9019S-SMT |  | PKMCS0909E4000-R1 | BUZZER | smt
C1, C16, C17 | 3 | ANY | 2u2 | C_0805_2012Metric |  |  | MLCC 0805 50V X7S/R | smt
C10 | 1 |  | 22u | C_0805_2012Metric |  |  | MLCC 0805 25V X7S/R | smt
C11 | 1 |  | 47n | C_0402_1005Metric |  |  | MLCC 0402 50V X7S/R | smt
C12, C21, C29, C3, C30, C31, C46, C47, C48, C49, C50, C51 | 12 |  | 1u | C_0402_1005Metric |  |  | MLCC 0402 50V X7S/R | smt
C13, C14, C15, C18, C19, C20, C22, C35 | 8 |  | 10µ 50V | C_1206_3216Metric |  |  | MLCC 1206 50V X7S/R | smt
C2 | 1 |  | DNP | CP_Elec_6.3x5.7 |  |  |  | smt
C23, C24, C25, C26, C27, C28, C32, C33, C37, C4, C5, C6, C7 | 13 |  | 100n | C_0402_1005Metric |  |  | MLCC 0402 50V X7S/R | smt
C34, C41, C42, C43, C44, C45, C8, C9 | 8 |  | 22µ 16V | C_0805_2012Metric |  |  | MLCC 0805 16V X7S/R | smt
C36 | 1 |  | 2.7n | C_0402_1005Metric |  |  | MLCC 0402 50V X7S/R | smt
C38 | 1 |  | DNP | C_0402_1005Metric |  |  |  | smt
C39 | 1 |  | 100p | C_0402_1005Metric |  |  | MLCC 0402 50V X7S/R | smt
C40 | 1 |  | DNP | C_0402_1005Metric |  |  |  | smt
D1, D3, D4 | 3 |  | SMAJ22A | D_SMA |  | SMAJ22A | TVS DIODE 400W | smt
D10 | 1 | NEXPERIA | PMEG6010CEJ | D_SOD-323F |  | PMEG6010CEJ | SCHOTTKY DIODE | smt
D11, D15, D17, D18, D19 | 5 |  | LED_R | LED_0402_1005Metric |  |  | LED 0402 RED | smt
D13 | 1 |  | LED_B | LED_0402_1005Metric |  |  | LED 0402 BLUE | smt
D14 | 1 |  | LED_G | LED_0402_1005Metric |  |  | LED 0402 GREEN | smt
D2, D7, D8 | 3 | NEXPERIA | BAS416,115 | D_SOD-323_HandSoldering |  | BAS416,115 | DIODE | smt
D9 | 1 | NEXPERIA | PMEG6010CEJ,115 | D_SOD-323 |  | PMEG6010CEJ,115 | SCHOTTKY DIODE | smt
F1 | 1 | SCHURTER | 3413.0328.24 | R_1206_3216Metric |  | 3413.0328.24 | FUSE 10A 35V SLOW | smt
H2, H4 | 2 | WUERTH | 9774010360 | Mounting_Wuerth_WA-SMSI-M3_H1mm_9774010360 |  | 9774010360 | WA SMSI M3 1MM | smt
J1 | 1 | TE CONNECTIVITY | 1-1827654-1 | 1-1827654-1 |  | 1-1827654-1 | CONNECTOR | tht
J10, J11, J13 | 3 | SAMTEC | CLP-102-02-F-D | PinSocket_2x02_P1.27mm_Vertical_SMD |  | CLP-102-02-F-D | PIN SOCKET | smt
J12 | 1 | JST | BM06B-GHS-TBT | JST_GH_BM06B-GHS-TBT_1x06-1MP_P1.25mm_Vertical |  | BM06B-GHS-TBT | JST GH 6PIN | smt
J2, J3, J5 | 3 | JST | BM03B-GHS-TBT | JST_GH_BM03B-GHS-TBT_1x03-1MP_P1.25mm_Vertical |  | BM03B-GHS-TBT | JST GH 3 PIN | smt
J8, J9 | 2 | SAMTEC | CLP-105-02-F-D | PinSocket_2x05_P1.27mm_Vertical_SMD |  | CLP-105-02-F-D | PIN SOCKET | smt
L1 | 1 | BOURNS | SRN5040-220M | L_Sunlord_SWPA5040S |  | SRN5040-220M | INDUCTOR 22uH 1.6A | smt
L2 | 1 | BOURNS | SRN6045TA-3R3Y | L_Bourns_SRN6045TA |  | SRN6045TA-3R3Y | INDUCTOR 3.3uH 5A | smt
Q1, Q5, Q6 | 3 | VISHAY | SIR180ADP-T1-RE3 | PowerPAK_SO-8_Single |  | SIR180ADP-T1-RE3 | NFET 60V 137A | smt
R1, R13, R17, R18, R19, R27, R28, R29 | 8 |  | 1k | R_0402_1005Metric |  |  | RESISTOR 1% 0402 | smt
R10, R14, R15, R52, R8 | 5 |  | 10k | R_0402_1005Metric |  |  | RESISTOR 1% 0402 | smt
R11 | 1 |  | 147k | R_0402_1005Metric |  |  | RESISTOR 1% 0402 | smt
R12 | 1 |  | DNP | R_0402_1005Metric |  |  |  | smt
R16 | 1 |  | 0R | R_0402_1005Metric |  |  | RESISTOR 1% 0402 | smt
R2 | 1 |  | DNP | R_0805_2012Metric_Pad1.20x1.40mm_HandSolder |  |  |  | smt
R20 | 1 |  | 33k | R_0402_1005Metric |  |  | RESISTOR 1% 0402 | smt
R21, R22 | 2 |  | 150k | R_0402_1005Metric |  |  | RESISTOR 1% 0402 | smt
R24, R3, R4, R5, R7, R9 | 6 |  | 100k | R_0402_1005Metric |  |  | RESISTOR 1% 0402 | smt
R55 | 1 | VISHAY | AC07000002008JAC00 | R_Axial_Power_L38.0mm_W6.4mm_P40.64mm |  | AC07000002008JAC00 | WIRE WOUND RESISTOR, MOUNT TIGHTLY ABOVE J1 | tht
R56 | 1 | VISHAY | WSLF25122L000FEA | R_2512_6332Metric |  | WSLF25122L000FEA | SHUNT 2mOhms | smt
R57 | 1 |  | 200k | R_0402_1005Metric |  |  | RESISTOR 1% 0402 | smt
R58 | 1 |  | 15.8k | R_0402_1005Metric |  |  | RESISTOR 1% 0402 | smt
R59 | 1 |  | 22k1 | R_0402_1005Metric |  |  | RESISTOR 1% 0402 | smt
R6 | 1 |  | 10R | R_0402_1005Metric |  |  | RESISTOR 1% 0402 | smt
R60 | 1 |  | 115k | R_0402_1005Metric |  |  | RESISTOR 1% 0402 | smt
R61 | 1 |  | 22.1k | R_0402_1005Metric |  |  | RESISTOR 1% 0402 | smt
R62, R63, R64, R65, R66, R67 | 6 |  | 330k | R_0402_1005Metric |  |  | RESISTOR 1% 0402 | smt
U1 | 1 | Chengdu Ebyte Elec Tech | E01-2G4M27S | XCVR_E01-2G4M27SX |  | E01-2G4M27S | NRF24L01P 2.4GHz 27dBm SPI Wireless Module | smt
U10 | 1 | DIODES INC | AP64500SP-13 | SOIC-8-1EP_3.9x4.9mm_P1.27mm_EP2.514x3.2mm |  | AP64500SP-13 | 40V 5A Sync. Buck | smt
U11 | 1 | CYNTEC | MUN12AD01-SH | Converter_DCDC_Cyntec_MUN12AD01-SH |  | MUN12AD01-SH | DC-DC Module 1V-5V 1A | smt
U12, U13, U14 | 3 | TEXAS INSTRUMENTS | TPS25200DRVR | WSON-6-1EP_2x2mm_P0.65mm_EP1x1.6mm_ThermalVias |  | TPS25200DRVR | EFUSE | smt
U2 | 1 | ANALOG DEVICES | AD8418BRMZ | MSOP-8_3x3mm_P0.65mm |  | AD8418BRMZ | Current Sense Amp | smt
U3, U4 | 2 | ANALOG DEVICES | LTC7004EMSE | MSOP-10-1EP_3x3mm_P0.5mm_EP1.68x1.88mm |  | LTC7004EMSE | NFET DRIVER | smt
U5 | 1 | TEXAS INSTRUMENTS | LP2980AIM5X-3.0/NOPB | SOT-23-5 |  | LP2980AIM5X-3.0/NOPB | LIN REG 3V FIXED | smt
U6 | 1 | ST MICROELECTRONICS | STM32G431CBT6 | LQFP-48_7x7mm_P0.5mm |  | STM32G431CBT6 | MICROCONTROLLER | smt
U7 | 1 | TEXAS INSTRUMENTS | LV2862YDDCT | SOT-23-6 |  | LV2862YDDCT | BUCK 600MA | smt
U9 | 1 | TEXAS INSTRUMENTS | TCAN330GDCNT | SOT-23-8 |  | TCAN330GDCNT | 3.3V CAN TRANSCEIVER | smt

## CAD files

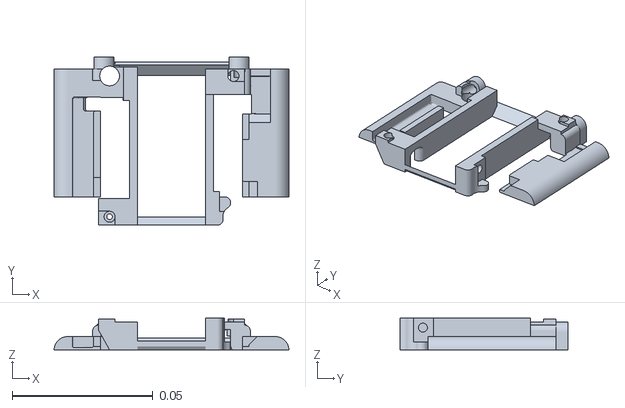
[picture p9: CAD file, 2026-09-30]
hardware/mechanical/meshes/electronics_frame_split_2-a.stl
0.0835 x 0.0598 x 0.0113

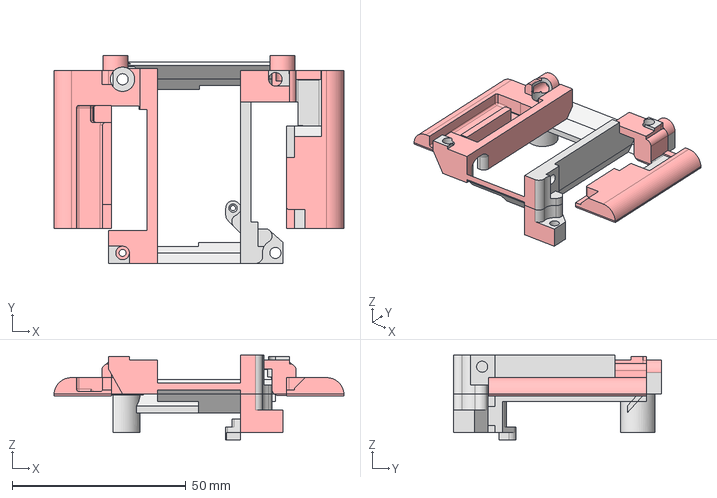
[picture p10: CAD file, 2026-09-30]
hardware/mechanical/step/electronics_frame_split_2.stp
83.5 x 59.8 x 24.4 mm

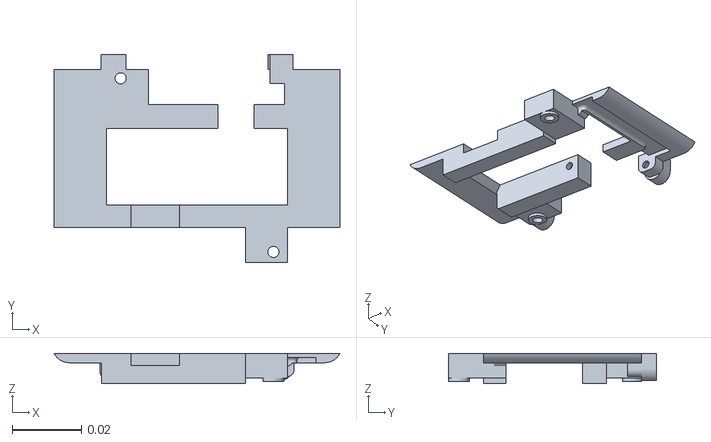
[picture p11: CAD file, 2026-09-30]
hardware/mechanical/meshes/electronics_frame_split_1-a.stl
0.0824 x 0.0598 x 0.0087

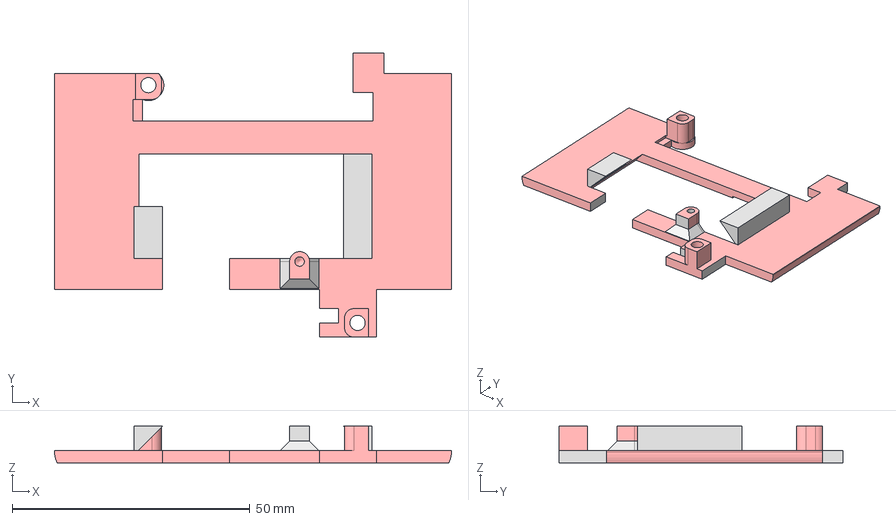
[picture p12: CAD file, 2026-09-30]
hardware/mechanical/step/electronics_frame_split_1-b.stp
83.5 x 59.8 x 7.70 mm

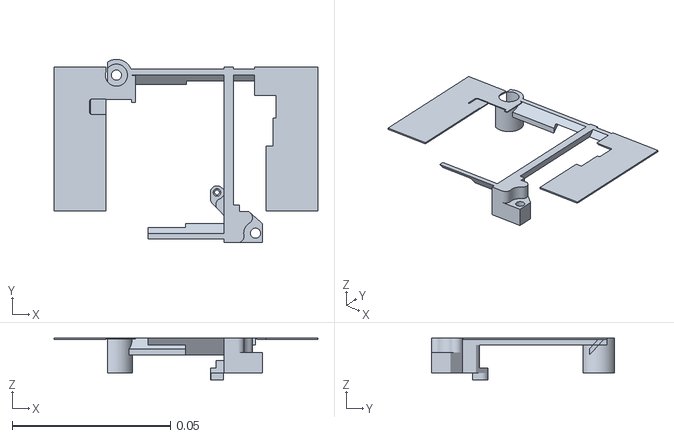
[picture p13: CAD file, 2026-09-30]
hardware/mechanical/meshes/electronics_frame_split_2-b.stl
0.0835 x 0.058 x 0.0132

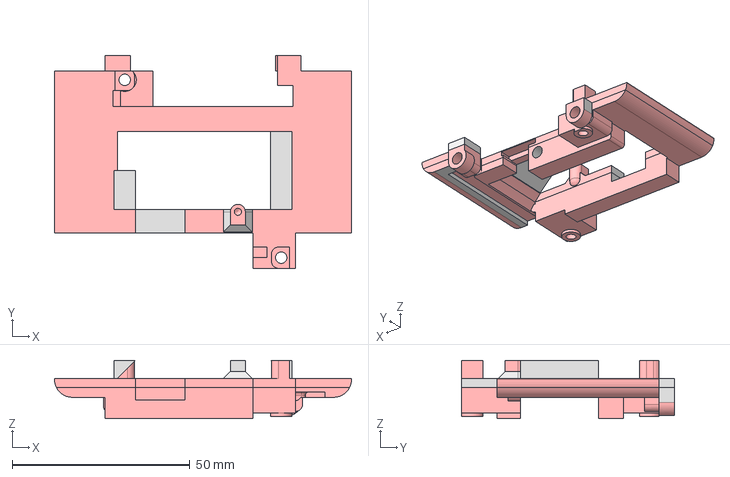
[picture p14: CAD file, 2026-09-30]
hardware/mechanical/step/electronics_frame_split_1.stp
83.5 x 59.8 x 16.4 mm

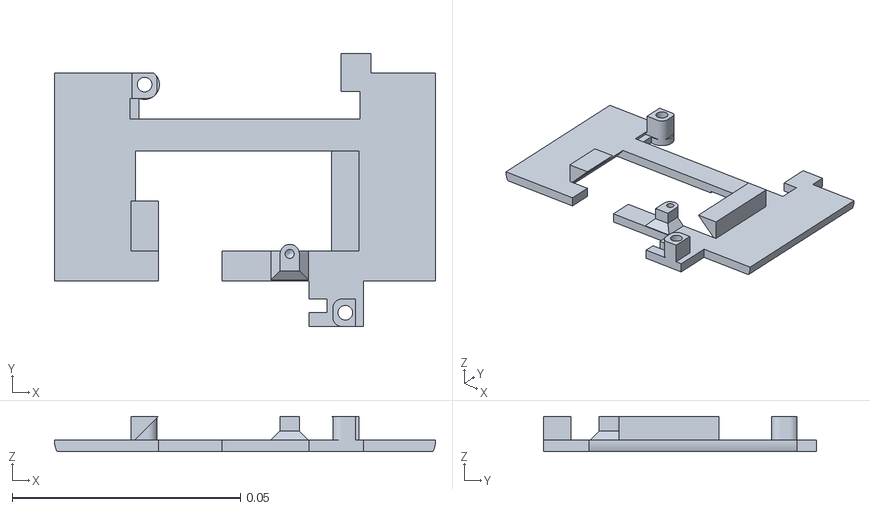
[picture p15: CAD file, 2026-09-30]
hardware/mechanical/meshes/electronics_frame_split_1-b.stl
0.0835 x 0.0598 x 0.0077

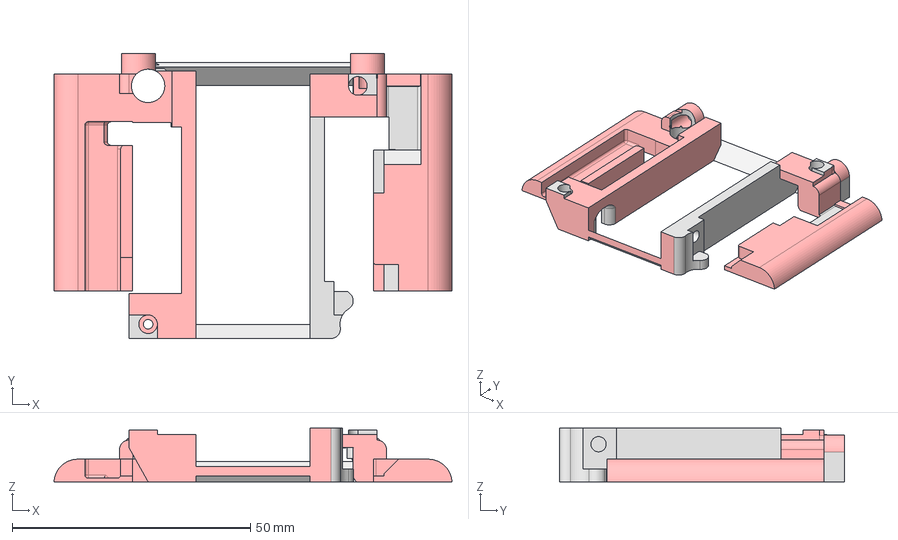
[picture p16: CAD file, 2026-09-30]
hardware/mechanical/step/electronics_frame_split_2-a.stp
83.5 x 59.8 x 11.2 mm

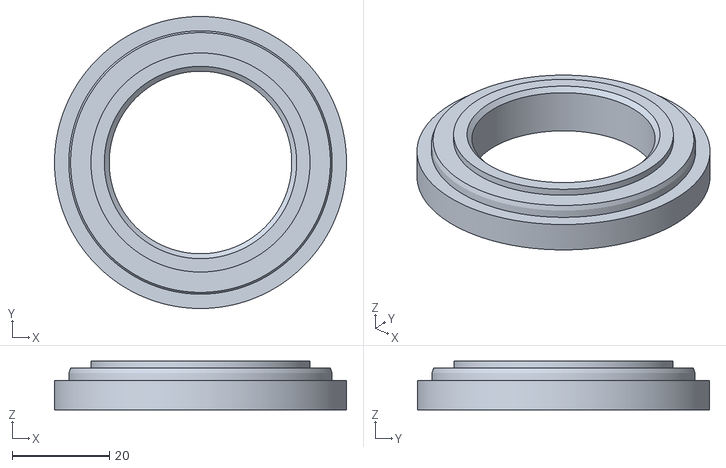
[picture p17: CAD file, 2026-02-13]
hardware/mechanical/meshes/motor_fixture_MN4006.stl
60.0 x 60.0 x 10.0

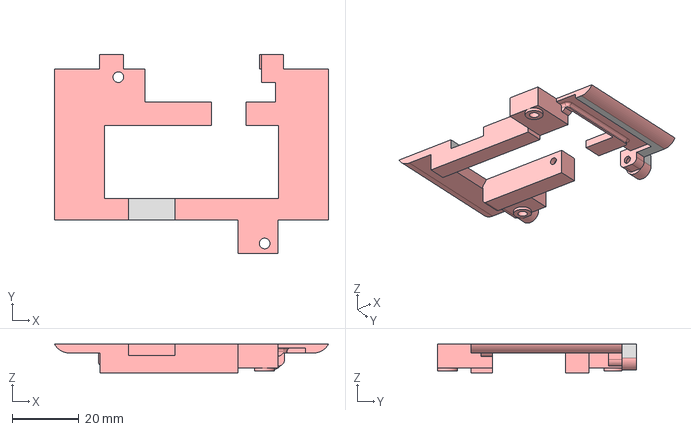
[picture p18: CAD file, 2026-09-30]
hardware/mechanical/step/electronics_frame_split_1-a.stp
82.4 x 59.8 x 8.70 mm

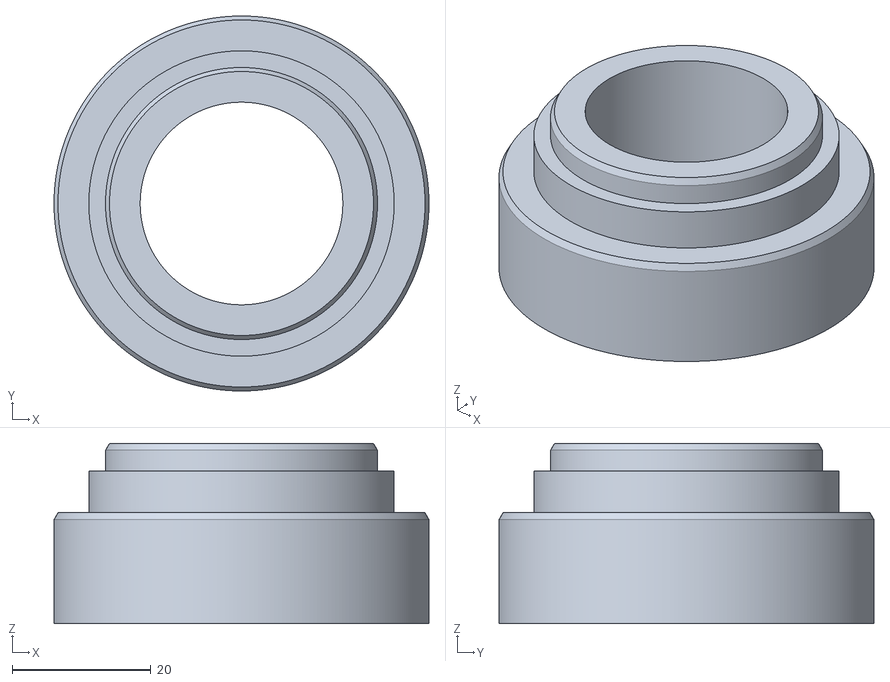
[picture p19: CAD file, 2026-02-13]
hardware/mechanical/meshes/motor_removal_punch_long.stl
54.0 x 54.0 x 26.0

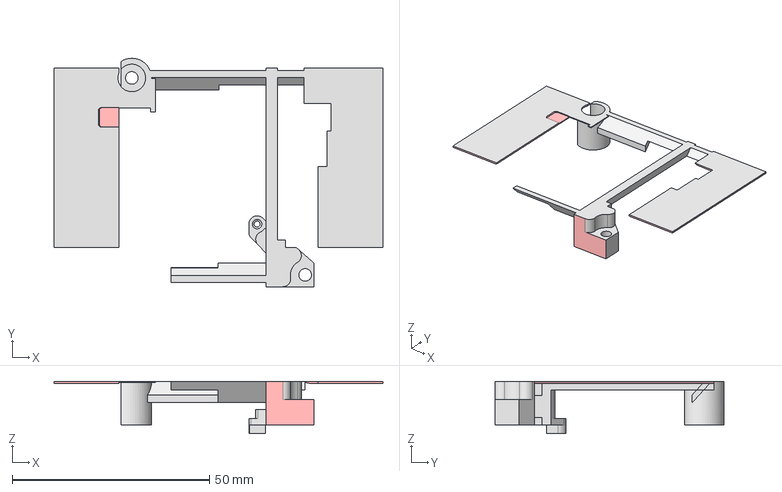
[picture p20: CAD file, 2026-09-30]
hardware/mechanical/step/electronics_frame_split_2-b.stp
83.5 x 58.0 x 13.2 mm

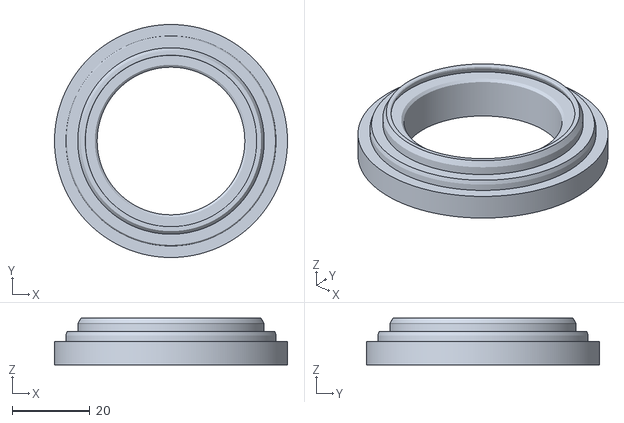
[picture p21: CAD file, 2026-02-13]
hardware/mechanical/meshes/motor_fixture_MN4006_EVO.stl
60.0 x 60.0 x 12.0

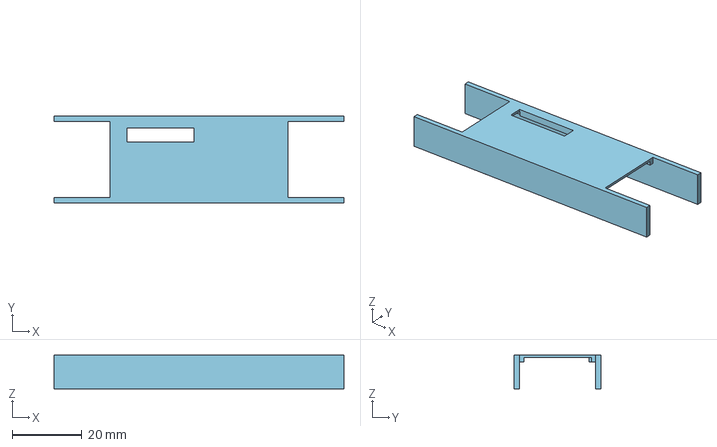
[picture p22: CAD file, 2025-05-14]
hardware/mechanical/step/battery_front.stp
83.0 x 24.8 x 9.60 mm

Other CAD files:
hardware/mechanical/meshes/motor_removal_punch_short.stl
hardware/mechanical/step/battery_back.stp
hardware/mechanical/meshes/motor_removal_fixture.stl
hardware/mechanical/step/reactionwheel.stp
hardware/mechanical/meshes/actuator_rotor.obj
hardware/mechanical/meshes/actuator_rotor.stl
hardware/mechanical/meshes/battery_back.stl
hardware/mechanical/meshes/battery_front.stl
hardware/mechanical/meshes/body.stl
hardware/mechanical/meshes/magnet_adapter.stl
hardware/mechanical/meshes/mini-wheelbot.stl
hardware/mechanical/step/frame.stp
hardware/mechanical/step/lid.stp

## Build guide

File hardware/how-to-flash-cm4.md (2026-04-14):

# Flashing the CM4 eMMC

This guide explains how to build the CM4 Buildroot image, flash it to the CM4 eMMC using the official CM4 IO board, and log in to the system for the first time.

## Materials needed

- CM4 with eMMC and Wi-Fi
- Official CM4 IO board
- Micro-USB cable for the CM4 IO board USB slave port (`J11`)
- Power supply for the CM4 IO board (`J19`)

## Configure default network and login credentials

The generated image is configured to:

- connect to Wi-Fi SSID `botnet` with password `botnet`
- use hostname `wheelbot`
- allow login as user `root` with password `wheelbot`

The Wi-Fi credentials are defined here:
[cm4-software/wheelbot_tree/board/common/wpa_supplicant.conf](cm4-software/wheelbot_tree/board/common/wpa_supplicant.conf)

The default root password is defined here:
[cm4-software/wheelbot_tree/configs/wheelbot_cm4_defconfig](cm4-software/wheelbot_tree/configs/wheelbot_cm4_defconfig)

If you do not want to ship images with these defaults, change them before building.

## Build the image on the host

Install the required Buildroot host packages from the [official Buildroot documentation](https://buildroot.org/downloads/manual/manual.html#requirement).

From the repository root, make sure the Buildroot submodule is present:

```bash
git submodule update --init --recursive hardware/cm4-software/buildroot
cd hardware/cm4-software/buildroot
```

Configure Buildroot for the Wheelbot CM4 image:

```bash
make defconfig BR2_DEFCONFIG=../wheelbot_tree/configs/wheelbot_cm4_defconfig
```

Build the image. The first build usually takes 20 to 60 minutes:

```bash
make BR2_EXTERNAL=/absolute/path/to/mini-wheelbot/hardware/cm4-software/wheelbot_tree
```

The flashable image will be written to:

```text
hardware/cm4-software/buildroot/output/images/sdcard.img
```

## Optional: build the image using Docker

If you prefer not to install the Buildroot host dependencies locally, you can use the provided Dockerfile.

From the repository root, build the container image:

```bash
docker build -t wheelbot-cm4-build -f hardware/cm4-software/docker/Dockerfile hardware/cm4-software/docker
```

Then run the Buildroot build inside the container:

```bash
docker run --rm -it \
  --user "$(id -u):$(id -g)" \
  -e HOME=/tmp \
  -v "$(pwd)/hardware/cm4-software:/work" \
  -w /work/buildroot \
  wheelbot-cm4-build \
  bash -lc 'make defconfig BR2_DEFCONFIG=../wheelbot_tree/configs/wheelbot_cm4_defconfig && make BR2_EXTERNAL=/work/wheelbot_tree'
```

This produces the same output image on the host at `hardware/cm4-software/buildroot/output/images/sdcard.img`.

## Flash the eMMC on the CM4

1. Put the CM4 on the official IO board.
2. Fit the `J2` jumper to disable normal eMMC boot and enable USB boot mode.
3. Connect the IO board to your computer with a micro-USB cable on `J11`.
4. Prepare power for the IO board on `J19`, but do not power it on yet.

The result should look like this:
<table align="center">
  <tr>
    <td align="center">
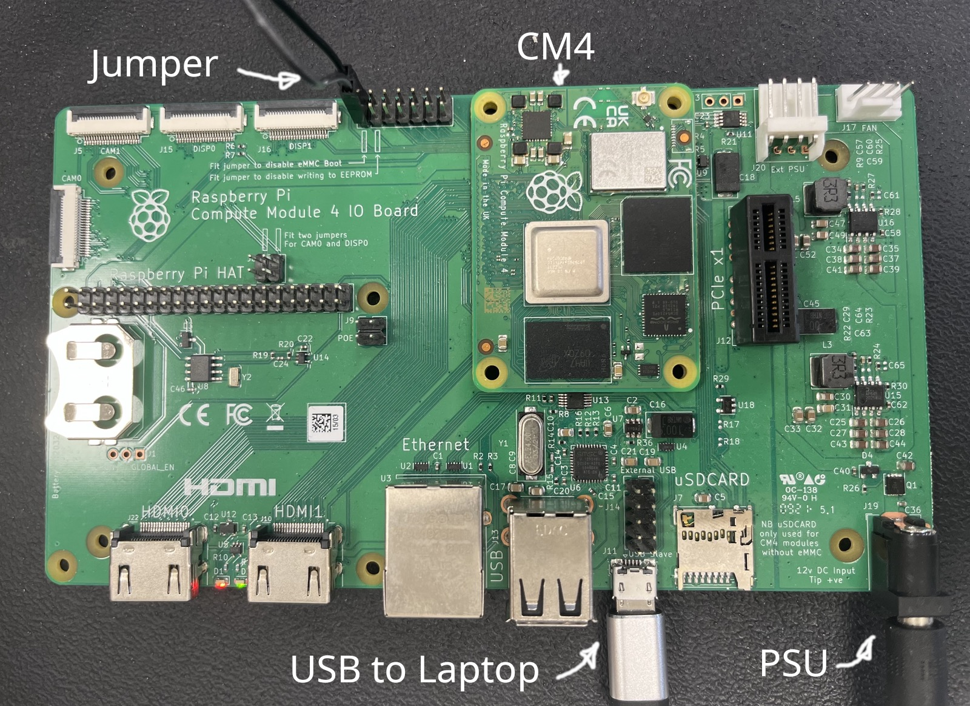
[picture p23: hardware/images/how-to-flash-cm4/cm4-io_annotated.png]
Annotated CM4 IO board for flashing
      <br/>
    </td>
  </tr>
</table>

You need [`rpiboot`](https://github.com/raspberrypi/usbboot) on your host to expose the eMMC as a block device.
You can either install it on your machine or use the copy built by Buildroot at `hardware/cm4-software/buildroot/output/host/bin/rpiboot`.

Start `rpiboot` on the host:

```bash
rpiboot
```

Then power on the CM4 IO board. You should see output similar to:

```text
$ rpiboot
RPIBOOT: build-date Jul 10 2023 version 20221215~105525 c4b12f85
Waiting for BCM2835/6/7/2711...
Loading embedded: bootcode4.bin
Sending bootcode.bin
Successful read 4 bytes
Waiting for BCM2835/6/7/2711...
Loading embedded: bootcode4.bin
Second stage boot server
Cannot open file config.txt
Cannot open file pieeprom.sig
Loading embedded: start4.elf
File read: start4.elf
Cannot open file fixup4.dat
Second stage boot server done
```

Identify the new block device with `lsblk`. A disk such as `/dev/sdX` should appear.
Make sure you pick the whole device and not one of its partitions.

If your desktop auto-mounted any partitions from the CM4 eMMC, unmount them before flashing.

From `hardware/cm4-software/buildroot/output/images`, write `sdcard.img` to the detected device:

```bash
cd hardware/cm4-software/buildroot/output/images
sudo dd if=sdcard.img of=/dev/sdX bs=64K status=progress conv=fsync
sync
```

After flashing finishes:

1. Power off the CM4 IO board.
2. Remove the `J2` jumper so the CM4 boots from eMMC again.
3. Disconnect the micro-USB cable.

## First boot and access

While the CM4 is still on the IO board, you can connect a monitor, keyboard, and mouse and verify that Buildroot boots.

After moving the CM4 to the Wheelbot compute carrier, it should connect to the configured Wi-Fi automatically and request an IP address via DHCP on `wlan0`.

You can then log in over SSH as `root`:

```bash
ssh root@<cm4-ip-address>
```

The default password is:

```text
wheelbot
```

If you do not know the IP address, check your router or scan the local network for hostname `wheelbot`.

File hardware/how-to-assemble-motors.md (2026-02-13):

# Assembling the Motors

## Prepare Parts and Fixtures
Depending on the motor version, use the matching 3D-printed fixture:
- motor_fixture_MN4006.stl fixture for MN4006
- motor_fixture_MN4006_EVO.stl fixture for MN4006 EVO

Have the following parts and tools ready:
- Brass wheel
- Motor rotor
- Fast-curing epoxy (for example, 5-minute epoxy)

Make sure the brass wheel bore and rotor outer surface are clean and free of grease before gluing.

## Disassemble Motor and Prepare Stator
Before bonding the wheel to the rotor, disassemble the motor so rotor and stator are separated.

After separating rotor and stator, solder the stator phases to JST-XH pre-crimp cables (depicted in [how-to-assemble-robot.md](how-to-assemble-robot.md)).

## Place Wheel in Fixture
Place the brass wheel in the fixture first.
Check that it sits fully seated and flat in the fixture.
If the wheel is tilted at this stage, the final assembly can become imbalanced.

For the MN4006 EVO version, snapping the rotor into the fixture can require noticeable force.
Apply force only in the intended insertion direction and avoid side loading.

<table align="center">
  <tr>
    <td align="center">
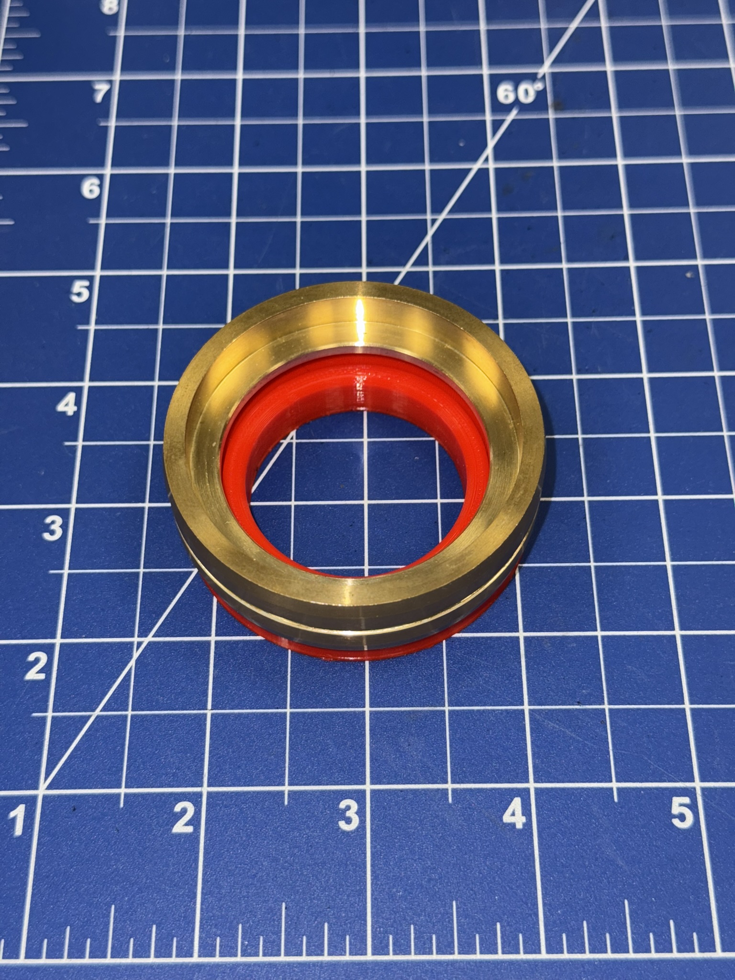
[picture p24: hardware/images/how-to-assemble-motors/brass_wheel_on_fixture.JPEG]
Brass wheel on assembly fixture
      <br/>
    </td>
  </tr>
</table>

## Apply Epoxy and Insert Rotor
Spread fast-curing epoxy around the outside of the rotor.
Use only as much as needed for a continuous thin bond line to avoid excessive squeeze-out.

Insert the rotor into the brass wheel while it is supported by the fixture.
During insertion, rotate the rotor slightly to distribute epoxy evenly over the full circumference.

Once the rotor is inserted, apply vertical pressure onto the rotor-wheel stack.
This seats both components to the correct axial position.

<table align="center">
  <tr>
    <td align="center">
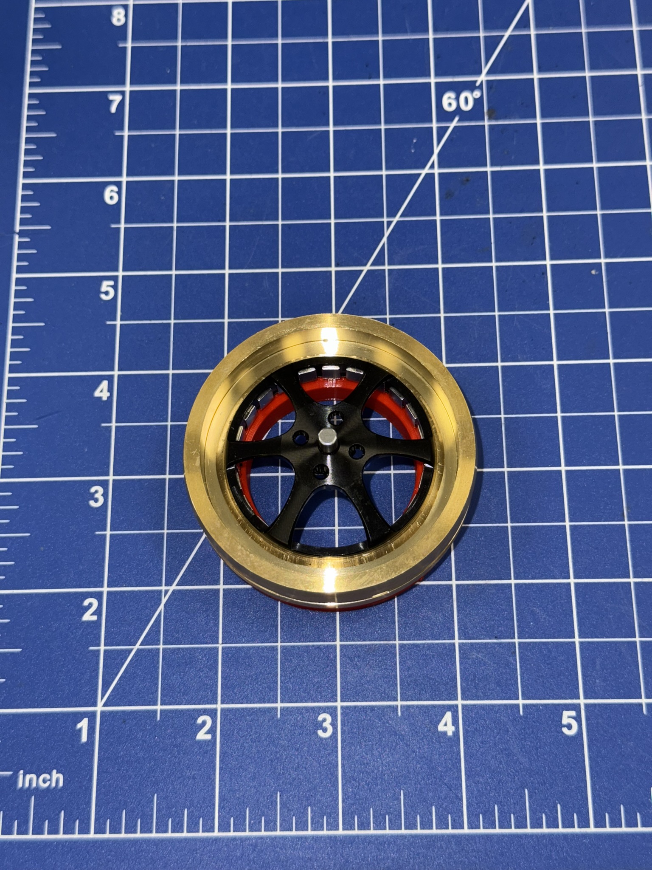
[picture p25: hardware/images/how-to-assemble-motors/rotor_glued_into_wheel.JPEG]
Rotor glued into brass wheel
      <br/>
    </td>
  </tr>
</table>

## Align and Check Flatness
With light downward preload still applied, rotate the brass wheel on the fixture.
Do this for two reasons:
1. To help spread epoxy uniformly around the interface.
2. To verify the wheel sits flat without wobble.

If you detect visible tilt or wobble before curing, correct alignment immediately.

## Let Epoxy Cure
Leave the assembly in the fixture and allow the epoxy to cure for the full time specified by the epoxy manufacturer.
Do not disturb the assembly during this period.

Avoid handling early, as partial cure can still cause misalignment.

<table align="center">
  <tr>
    <td align="center">
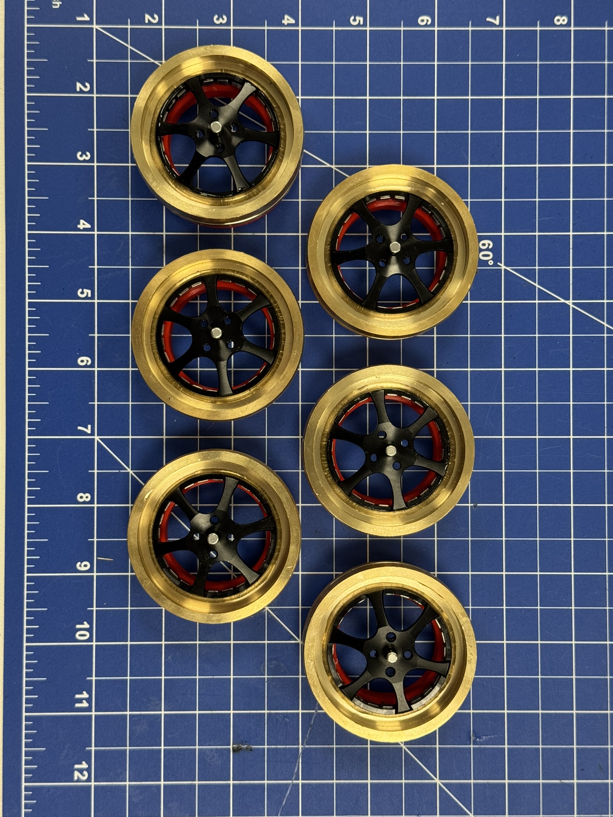
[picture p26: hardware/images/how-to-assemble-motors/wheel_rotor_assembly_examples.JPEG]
Wheel rotor assembly examples
      <br/>
    </td>
  </tr>
</table>

## Remove Fixture
After full cure, remove the fixture from the rotor-wheel assembly.
This can require some force if epoxy has spilled onto the fixture.

Do not reuse the 3D-printed fixture for another wheel-rotor assembly.
Glue residues can alter alignment and reduce repeatability on future builds.

## Rework an Imbalanced Assembly
If the wheel-motor assembly is imbalanced, press the rotor back out of the brass wheel using the motor removal fixture and punches.

Use this sequence:
1. Use the short punch first to break the epoxy bond.
2. Then use the long punch to fully press the rotor out of the wheel.

After disassembly, clean residual adhesive from mating surfaces before attempting a new assembly.

<table align="center">
  <tr>
    <td align="center">
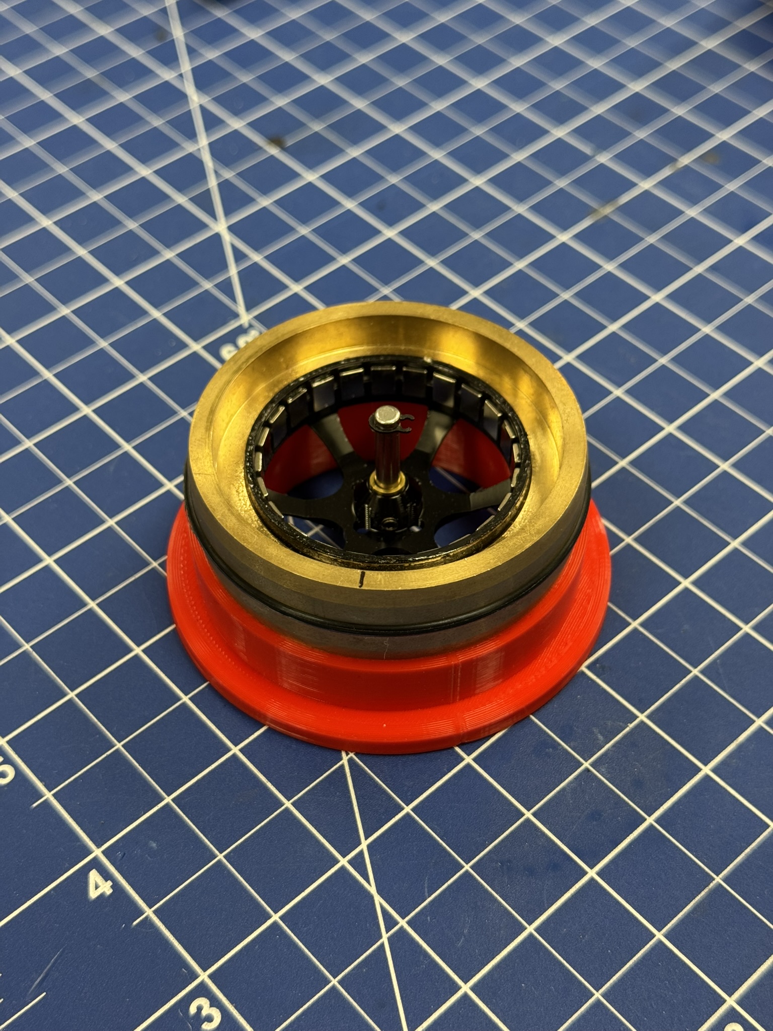
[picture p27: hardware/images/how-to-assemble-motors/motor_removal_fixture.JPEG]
Motor removal fixture
      <br/>
    </td>
    <td align="center">
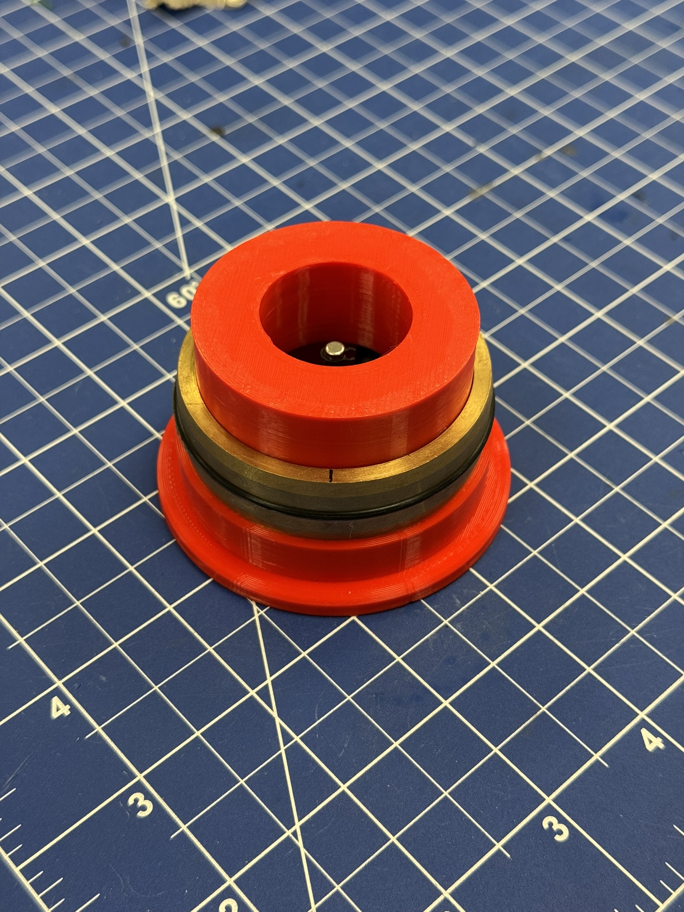
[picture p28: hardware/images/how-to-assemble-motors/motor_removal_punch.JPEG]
Motor removal punches
      <br/>
    </td>
    <td align="center">
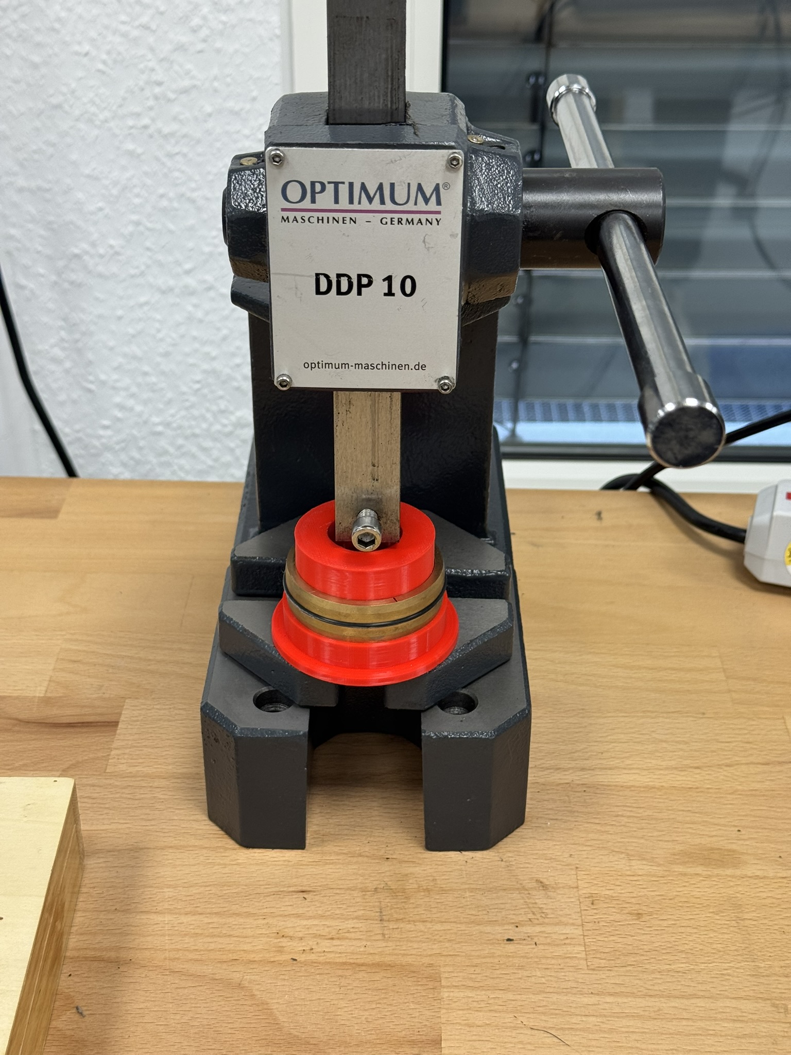
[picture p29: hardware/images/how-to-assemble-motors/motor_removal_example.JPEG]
Motor removal example
      <br/>
    </td>
  </tr>
</table>

## Reinforce Second Side of the Bond and Reassemble Motor
After the first bond has cured and alignment is confirmed, reinforce the second side of the rotor-wheel bond.
Spread epoxy along the outer edge between rotor and wheel to create a secondary fillet bond.
This can be done best using a syringe and a flat wide-lumen needle.

Let this reinforcement epoxy cure for the full time specified by the manufacturer.
After curing, reassemble the rotor-wheel assembly with the stator.

<table align="center">
  <tr>
    <td align="center">
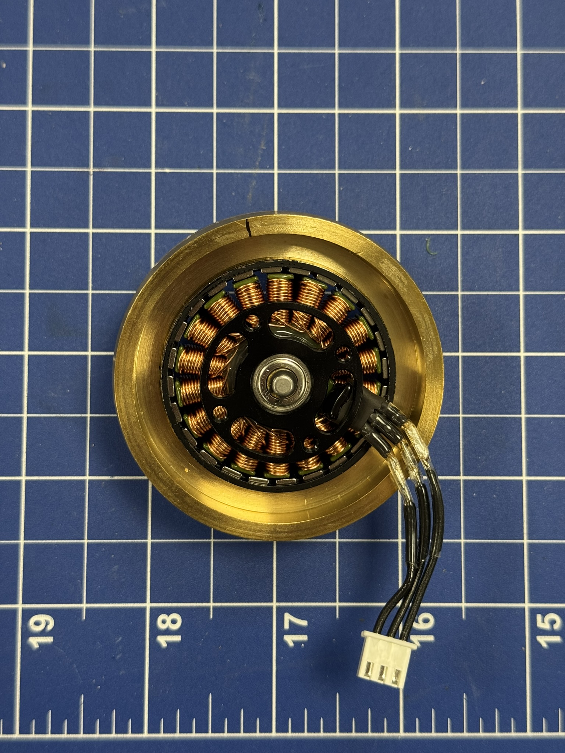
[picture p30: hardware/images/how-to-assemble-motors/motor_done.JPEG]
Final motor reassembled
      <br/>
    </td>
  </tr>
</table>

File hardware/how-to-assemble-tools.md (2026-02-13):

# Assembling the Tools

This guide explains how to assemble the three tool connectors listed in the Tools section of the [bill-of-materials.md](bill-of-materials.md):
- ST-Link V2 SWD adapter cable
- TTL-to-USB UART adapter cable
- USB-to-CAN adapter cable

## General Notes
Use JST-GH 6in precrimped wires and JST GH 3-pin housings.
Each adapter uses one 3-pin JST-GH cable.

Before plugging into any PCB:
- Verify pin order at the JST-GH connector.
- Verify continuity from tool-side pin to JST-GH contact.
- Avoid short circuits between adjacent pins.

## Assemble ST-Link V2 Adapter Cable
Prepare 3 wires:
1. Take 3 female jumper wires.
2. Cap/insulate one end of each jumper as needed.
3. Solder the other end of each jumper wire to 3 JST-GH 6in precrimp wires.
4. Add insulation (for example heat shrink) over each solder joint.

Insert the 3 JST-GH crimp contacts into one JST GH 3-pin housing.
Then connect the 3 female jumper ends to the ST-Link V2 pins:
- `SWCLK`
- `SWDIO`
- `GND`

Arrange the three wires in the JST-GH housing such that the final JST-GH pinout matches the SWD header pinout on the Mini Wheelbot PCBs.

<table align="center">
  <tr>
    <td align="center">
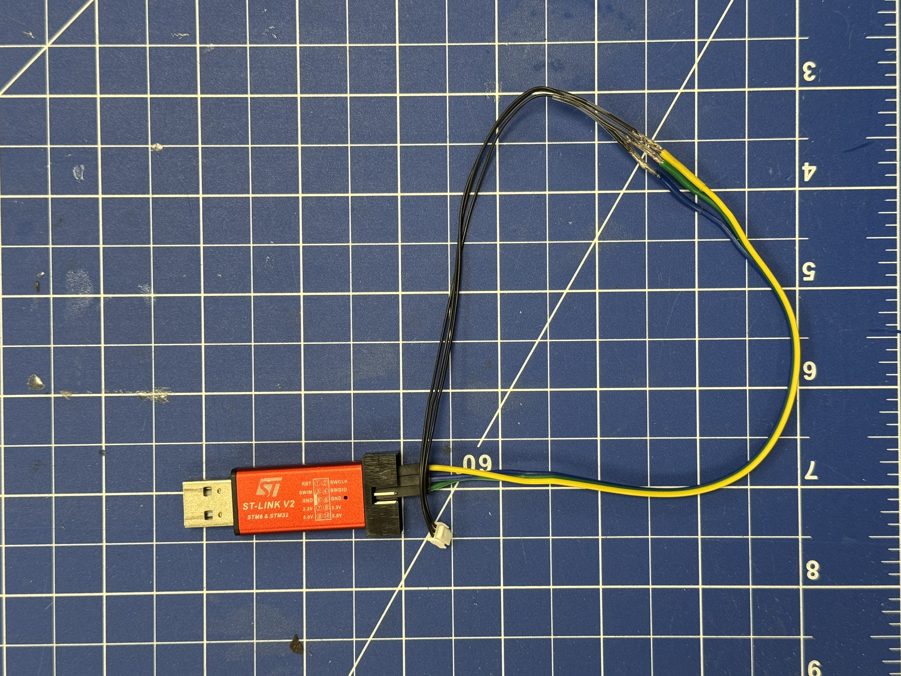
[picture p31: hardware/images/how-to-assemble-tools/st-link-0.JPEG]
ST-Link cable assembly step 1
      <br/>
    </td>
    <td align="center">
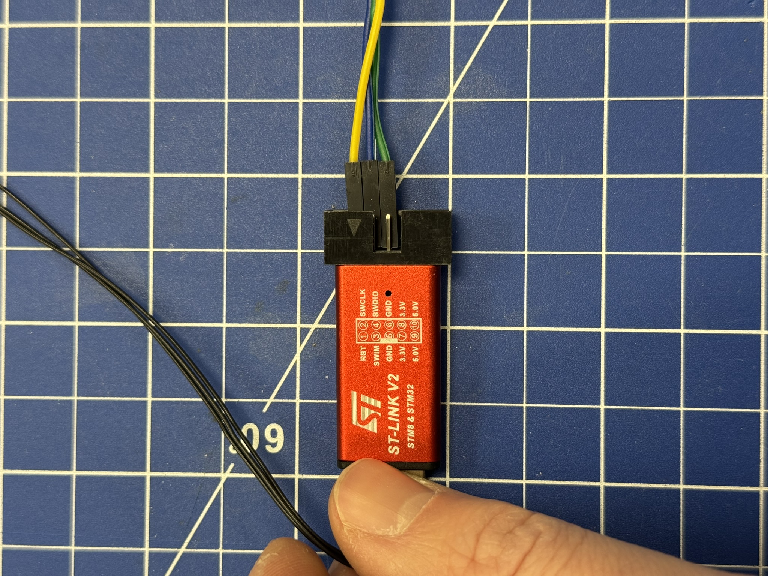
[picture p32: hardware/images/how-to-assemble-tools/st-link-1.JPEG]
ST-Link cable assembly step 2
      <br/>
    </td>
    <td align="center">
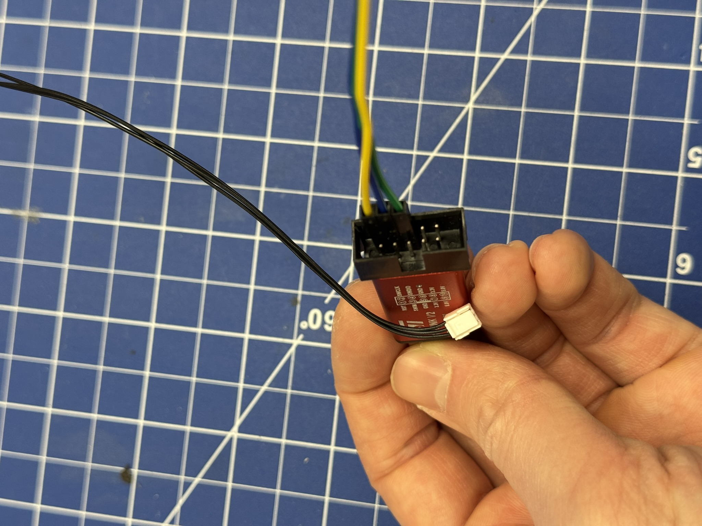
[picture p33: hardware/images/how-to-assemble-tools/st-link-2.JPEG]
ST-Link cable assembly final
      <br/>
    </td>
  </tr>
</table>

## Assemble UART Adapter Cable
Prepare 3 wires in the same way as for the ST-Link cable:
1. Take 3 female jumper wires.
2. Cap/insulate one end.
3. Solder to 3 JST-GH 6in precrimp wires.
4. Insulate each solder joint.

Insert the JST-GH crimps into one JST GH 3-pin housing.
Then connect the jumper ends to the TTL-to-USB adapter pins:
- `TXD`
- `RXD`
- `GND`

Arrange the JST-GH pin order so it matches the PCB UART header.
If communication does not work, check TX/RX orientation first.

<table align="center">
  <tr>
    <td align="center">
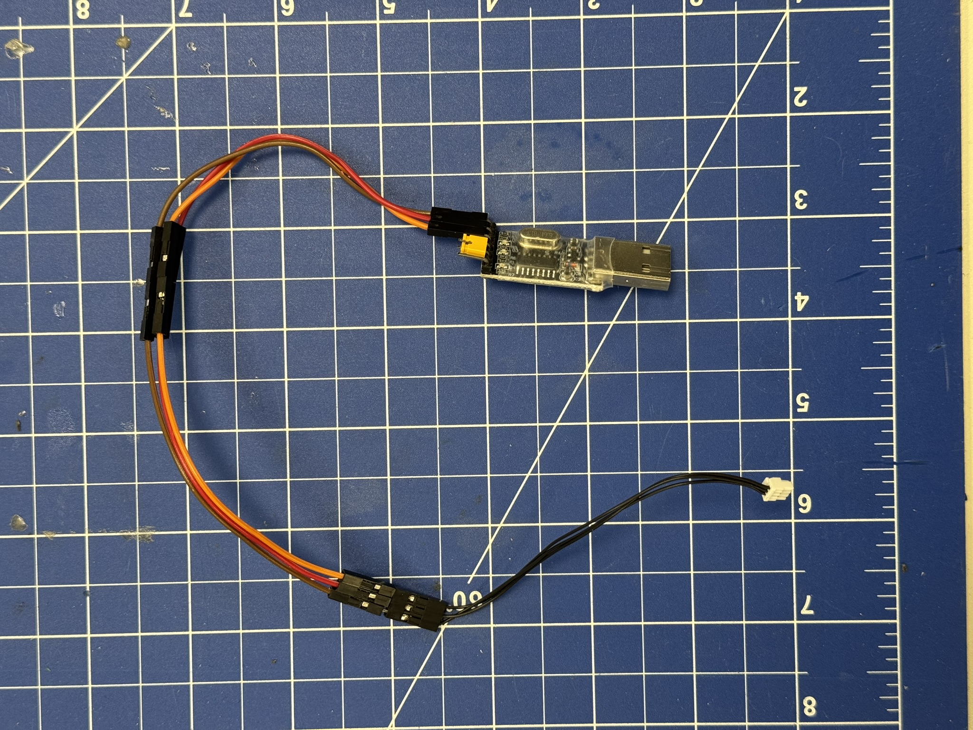
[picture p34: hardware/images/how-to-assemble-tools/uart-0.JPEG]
UART cable assembly step 1
      <br/>
    </td>
    <td align="center">
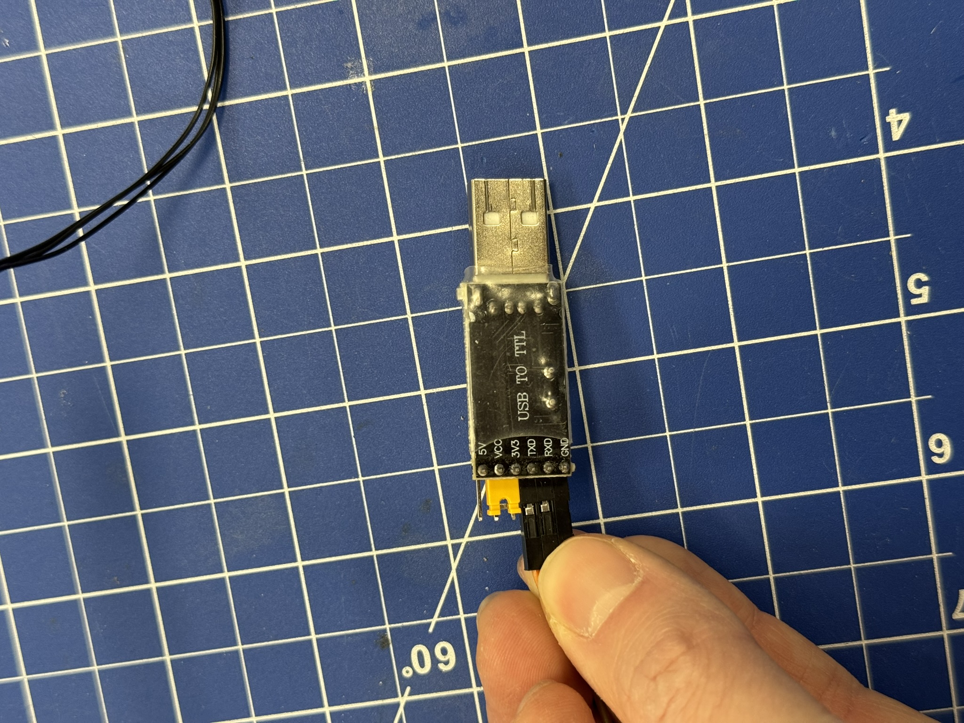
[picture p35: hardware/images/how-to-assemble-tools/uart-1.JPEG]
UART cable assembly final
      <br/>
    </td>
  </tr>
</table>

## Assemble CAN Adapter Cable
Assemble the USB-to-CAN adapter with the CAN pin terminal first.

Prepare the JST-GH side:
1. Take 3 JST-GH 6in precrimp wires.
2. Insert them into one JST GH 3-pin housing.

Connect the wire ends to the CAN pin terminal as:
- `CANL`
- `CANH`
- `GND`

Arrange the JST-GH pin order so this mapping matches the CAN header pinout on the Mini Wheelbot PCBs.

<table align="center">
  <tr>
    <td align="center">
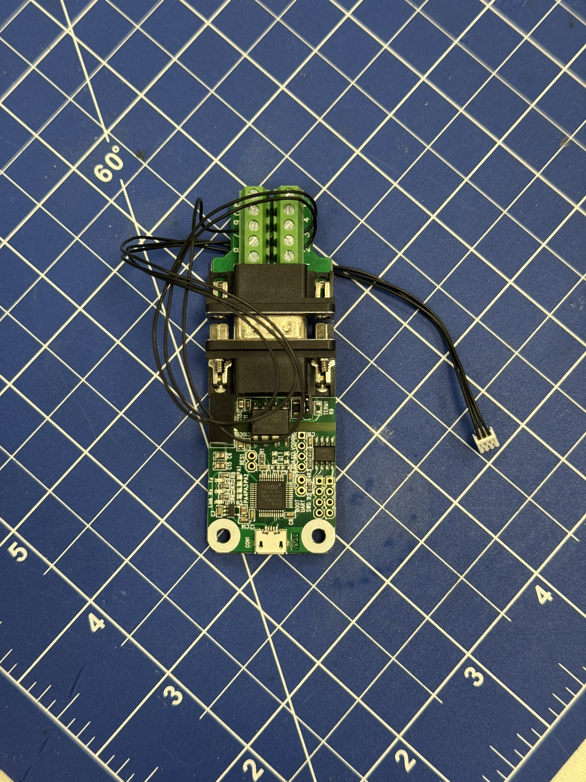
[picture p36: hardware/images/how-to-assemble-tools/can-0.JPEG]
CAN adapter assembly step 1
      <br/>
    </td>
    <td align="center">
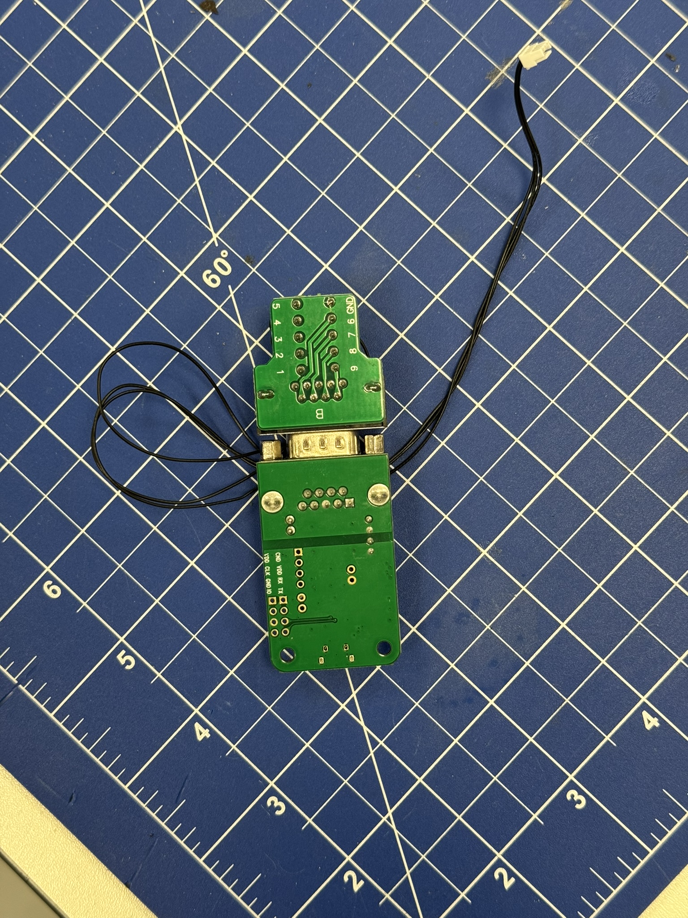
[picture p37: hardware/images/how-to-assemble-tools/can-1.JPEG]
CAN adapter assembly step 2
      <br/>
    </td>
    <td align="center">
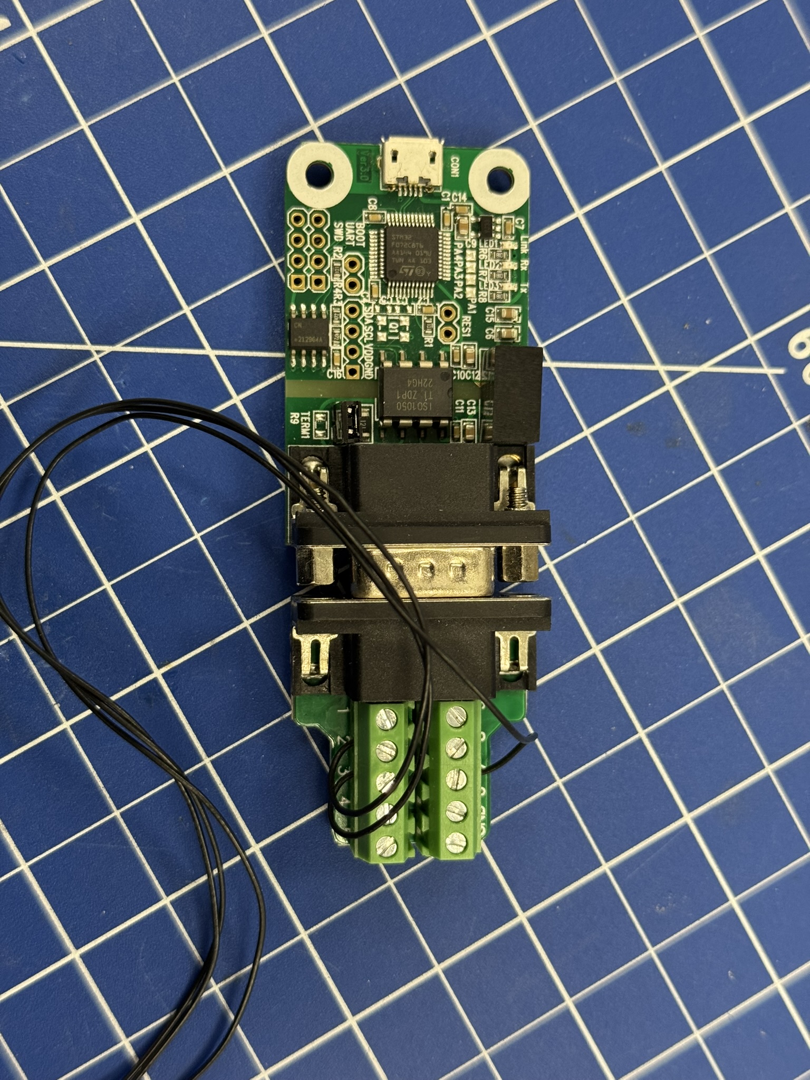
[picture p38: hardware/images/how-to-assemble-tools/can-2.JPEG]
CAN adapter assembly final
      <br/>
    </td>
  </tr>
</table>

## Final Check
For each assembled adapter cable:
1. Check connector orientation against the PCB silkscreen before first use.
2. Verify pin mapping and continuity with a multimeter.
3. Common failures during flashing are broken cables, jumpers not connected, wiring mixed up.

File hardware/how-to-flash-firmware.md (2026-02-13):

# Flashing Firmware to the PCBs

This guide explains how to flash the shipped firmware to the three STM32 microcontrollers:
- 1x on the power distribution board
- 2x on the motor controller boards

## OpenOCD on Linux (Short Introduction)
OpenOCD (Open On-Chip Debugger) is used to program STM32 microcontrollers via SWD, for example with an ST-Link V2.

Install OpenOCD on Linux:

```bash
sudo apt update
sudo apt install -y openocd
```

You will also need:

```bash
sudo apt install -y can-utils picocom
```

`can-utils` is used for `cansend` and `picocom` is used for UART log output.

## 1. Flash the Power Distribution Board

### Hardware Setup (Robot Not Assembled)
1. Connect the charging PCB to the power distribution board.
2. Do not connect motor controller boards yet.
3. Connect the battery to the power distribution board.
4. Connect the ST-Link adapter, UART adapter, and CAN adapter to the corresponding headers on the power distribution board.
5. Power on using the ON/OFF switch on the charging PCB.

<table align="center">
  <tr>
    <td align="center">
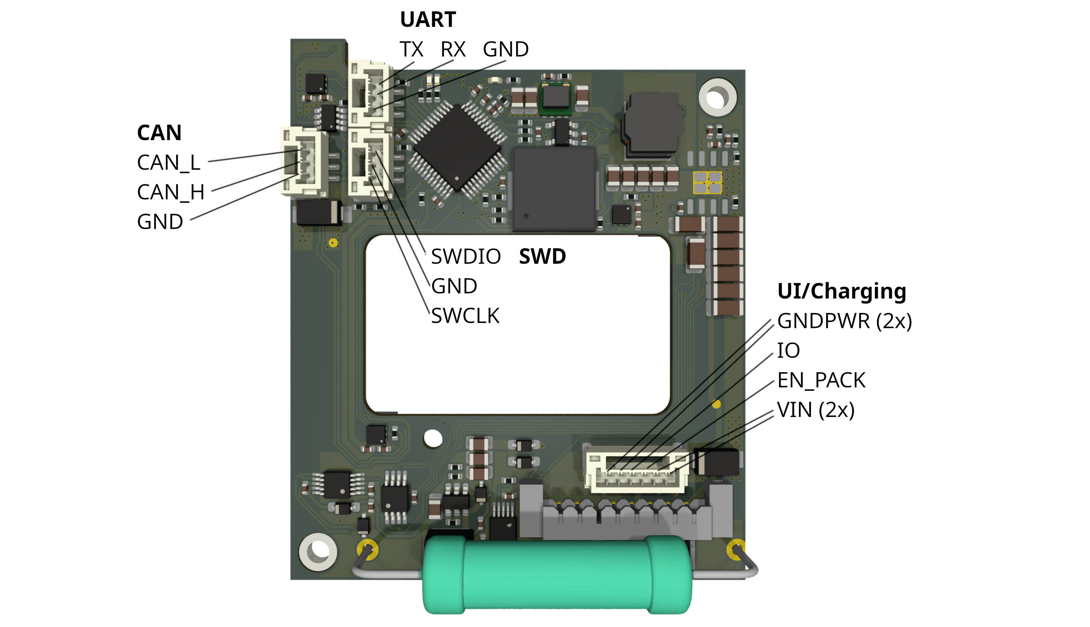
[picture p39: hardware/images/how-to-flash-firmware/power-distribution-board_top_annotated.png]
Power distribution board top annotated
      <br/>
    </td>
    <td align="center">
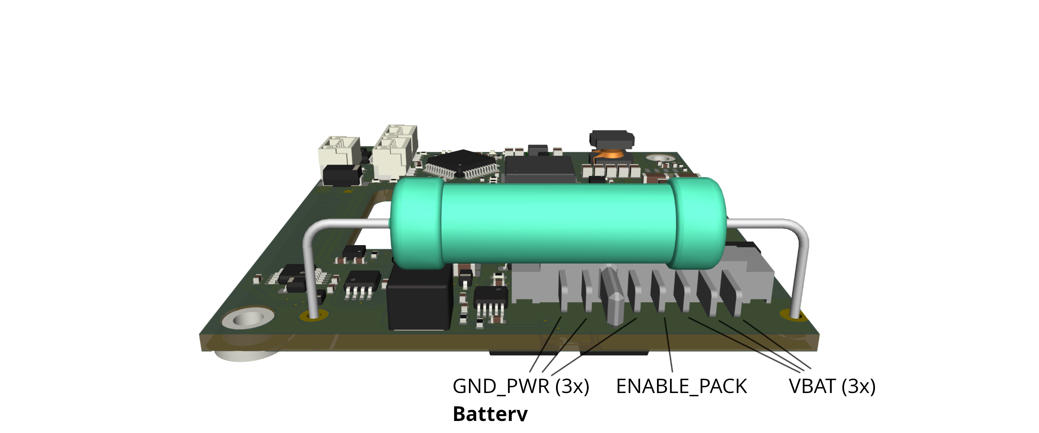
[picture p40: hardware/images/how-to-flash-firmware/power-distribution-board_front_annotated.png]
Power distribution board front annotated
      <br/>
    </td>
    <td align="center">
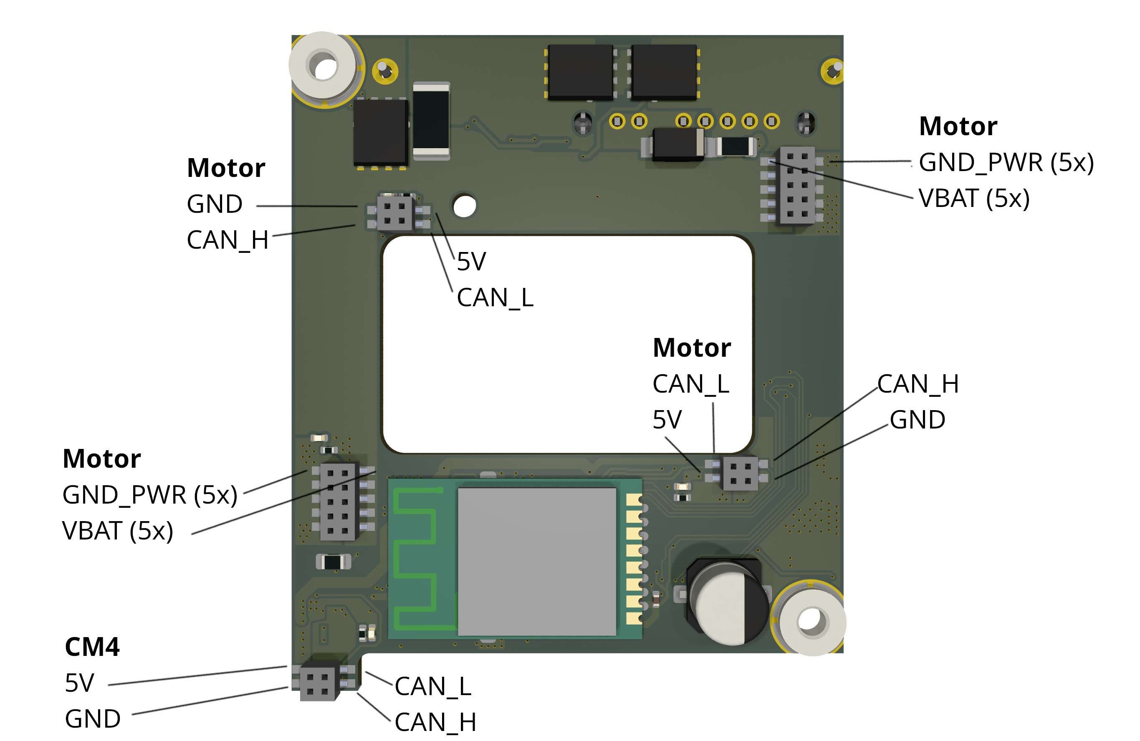
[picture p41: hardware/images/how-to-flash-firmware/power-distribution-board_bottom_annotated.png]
Power distribution board bottom annotated
      <br/>
    </td>
  </tr>
</table>

### Flash Command
Flash `power-distribution.elf`:

```bash
openocd \
  -f interface/stlink.cfg \
  -f target/stm32g4x.cfg \
  -c "program microcontroller-software/power-distribution.elf verify reset exit"
```

### Verify via UART
After flashing, power-cycle the power distribution board and check UART logs:

```bash
picocom /dev/ttyUSB0 -b 460800 --imap lfcrlf
```

If UART output appears after power-cycle, flashing of the power distribution board is complete.

## 2. Flash the Motor Controllers

### Hardware Setup
1. Turn battery power off.
2. Connect both motor controller boards to the power distribution board.
3. Keep the CAN adapter connected to the power distribution board.
4. Connect ST-Link and UART adapters to one motor controller board.
5. Power on the system using the ON/OFF switch on the charging PCB.

At this point, motor controllers are not powered yet.

<table align="center">
  <tr>
    <td align="center">
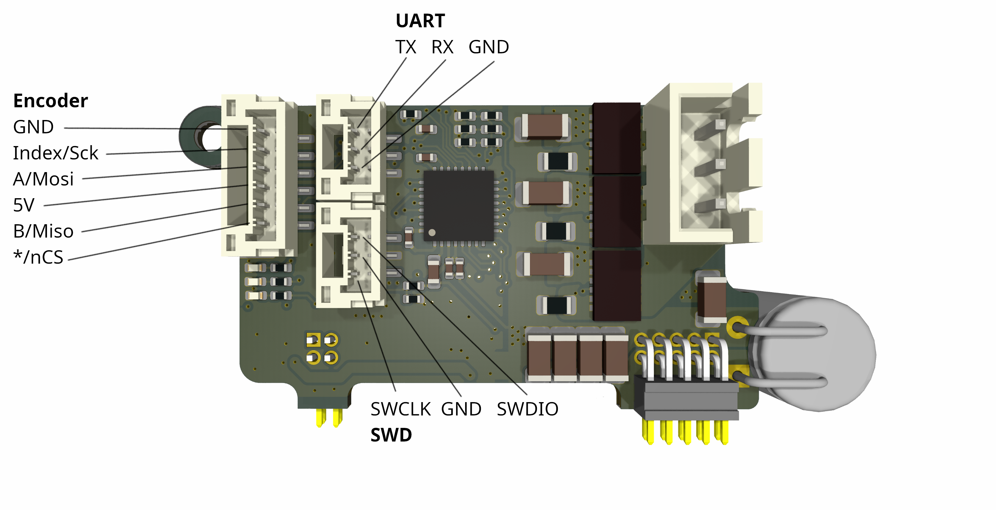
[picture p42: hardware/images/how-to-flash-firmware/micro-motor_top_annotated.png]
Micro motor controller top annotated
      <br/>
    </td>
    <td align="center">
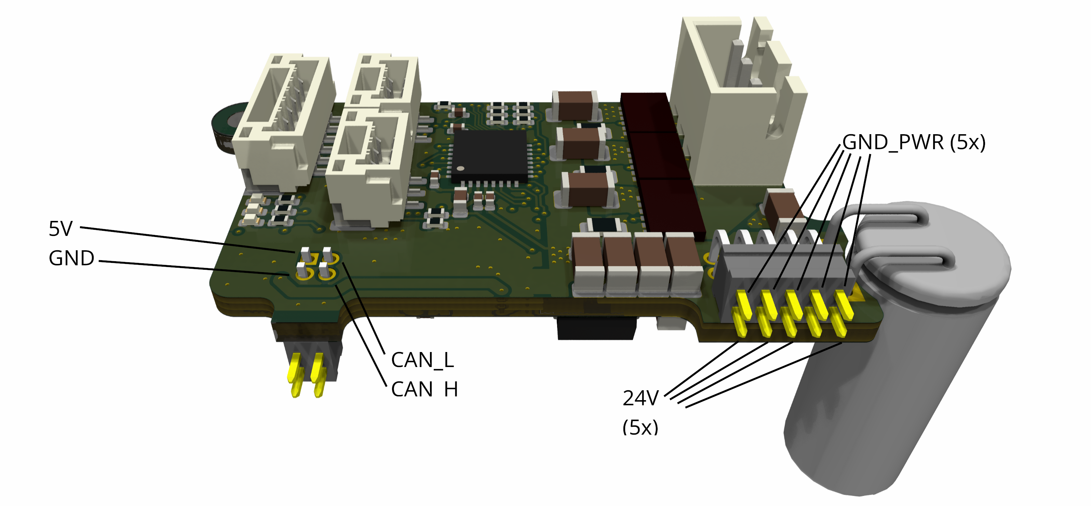
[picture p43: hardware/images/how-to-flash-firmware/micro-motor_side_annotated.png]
Micro motor controller side annotated
      <br/>
    </td>
  </tr>
</table>

### Enable Motor Controller Power via CAN
Bring up CAN and enable motor controller power:

```bash
ip link set can0 type can bitrate 1000000 && ip link set up can0
cansend can0 040#02
```

For CAN message details, see [how-to-set-motor-controller-IDs.md](how-to-set-motor-controller-IDs.md).

### Set BOOT0 Option
Run:

```bash
openocd -f interface/stlink.cfg -c "transport select hla_swd" -f target/stm32g4x.cfg -c "reset_config none" -c "init" -c "stm32g4x option_write 0 0x20 0x00000000 0x04000000" -c "shutdown"
```

### Flash Firmware
Flash `micro-motor.elf`:

```bash
openocd \
  -f interface/stlink.cfg \
  -f target/stm32g4x.cfg \
  -c "program microcontroller-software/micro-motor.elf verify reset exit"
```

### Wipe Motor Controller Config Region
Run:

```bash
openocd -f interface/stlink.cfg -f target/stm32g4x.cfg   -c "init"   -c "reset halt"   -c 'flash erase_address 0x08070000 0x00010000'   -c 'flash fillw 0x08070000 0x00000000 16384'   -c "reset run"   -c "exit"
```

Repeat the motor controller flashing steps for the second motor controller board.

### Verify via UART

If UART output appears after power-cycle, flashing of the motor controller board is complete. Remember, that in order to power the motor controllers, one has to send a can command.
To power cycle the motor controllers without power-cycling the power distribution board, send these two commands with short delay.
```bash
cansend can0 040#01
cansend can0 040#02
```

## 3. Next Step: Set Motor Controller IDs
After both motor controller boards are flashed, the PCBs are ready to be assembled.

Motor controller IDs can be set either:
- outside of the robot with external CAN adapter:
  [setMotorControllerIDs_external.py](../wheelbot-lib/scripts/micro-motor/setMotorControllerIDs_external.py)
- after assembly on the CM4:
  [setMotorControllerIDs_cm4.py](../wheelbot-lib/scripts/micro-motor/setMotorControllerIDs_cm4.py)

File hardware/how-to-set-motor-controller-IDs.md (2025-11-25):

# Motor Controller ID Assignment Tutorial

This guide explains how the `setMotorControllerIDs.py` script in `/wheelbot-lib/scripts/micro-motor/` operates and what steps are performed to assign CAN IDs to the motor controllers on the Mini Wheelbot.  
Follow these steps if you want to manually set the board IDs.

---

## Reference: ID Assignment Command Meanings

| Command | Example Frame | Description |
|---|---|---|
| `040#01` | `040#01` | Disable drive and logic power to both boards |
| `040#02` | `040#02` | Enable drive and logic power to both boards |
| `040#03xxxx` | `040#03000000` | Disable drive and logic power to both boards |
| `040#03000001` | `040#03000001` | Enable logic power only for board 1 |
| `040#03000100` | `040#03000100` | Enable logic power only for board 2 |
| `040#03010000` | `040#03010000` | Enable drive power and disable logic power to both boards |
| `040#03010101` | `040#03010101` | Enable drive and logic power to both boards |
| `000#` | `000#` | SYNC — request boards to respond |
| `020+ID#43` | `021#43`, `022#43` | Request UUID from board |
| `020+ID#00<UUID>00<newID>` | `021#00xxxxxxxx0001` | Assign new CAN ID |
| `020+newID#21` | `021#21`, `022#21` | Save new board ID to flash |

---

This ReadMe gives can commands with arbitration IDs based on the final state, where motor controller 1/2 have ID=1/2. After initial flash of the motor controller, these IDs are not set yet. In this state, the current board ID can be retrieved by sending a Sync message (000#), the response arbitration ID is 0x80 + {current board ID}. 
For example, a response arbitration ID of 0x17F corresponds to 0x80+0xFF, so {current board ID}= 0xFF = 255. 
Then, all can commands that communicate to the motor controller are sent with arbitration ID 0x20 + {current board ID}.

## Setup

The CAN interface on the Mini Wheelbot CM4 is called `motorCan`.

Run ID assignment script from the CM4:

```
python3 setMotorControllerIDs.py
```

---

## 1. Connect to the Mini Wheelbot

```
ssh root@<robot-ip>
```

---

## 2. Disable Logic Power to Both Motor Controllers

Ensures no conflicting responses during ID assignment:

```
cansend motorCan 040#03000000
```

## 3. Enable Logic Power for only Board 1

This isolates the first controller:

```
cansend motorCan 040#03000001
```

## 4. Request Board response

Send SYNC:

```
cansend motorCan 000#
```

Expected response shown via candump motorCan (exemplary):

```
081#
```

➡︎ Means a board currently has ID 0x01. Response arbitration ID is 080 + board ID. 

If no response, check wiring and power.
## 5. Request UUID From the Active Board

```
cansend motorCan 021#43
```

Board replies with 5 data bytes, e.g.:

```
0x01 AA BB CC DD
```

Where AABBCCDD = unique UUID.
## 6. Assign New Board ID Using UUID

Example: Assign ID 0x01 to this board

```
cansend motorCan 021#00AABBCCDD0001
```

## 7. Save Assigned ID to Flash

```
cansend motorCan 021#21
```

Wait ~2 seconds — do not power-cycle during this time.
Now Board 1 successfully stored the new ID.

## 8. Repeat Steps 2–7 for Board 2

Enable only board 2 logic power:

```
cansend motorCan 040#03000100
```

Then perform:

```
cansend motorCan 000#
cansend motorCan 022#43
cansend motorCan 022#00<UUID>0002
cansend motorCan 022#21
```

## 9. Verify Both Boards Respond on CAN

Send SYNC again:

```
cansend motorCan 040#03000101
cansend motorCan 000#
```

Expected:

```
081#
082#
```

If yes → IDs are correctly assigned.
## 10. Disable Logic Power After Completion

```
cansend motorCan 040#01
```

This prevents accidental motor activation.
You may now proceed with motor calibration

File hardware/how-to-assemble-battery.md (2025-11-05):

# Assembling the Battery

## Disassemble Packs
Make sure all cells are in approximately the same state of charge, when you assemble the packs.
The cell protection PCB does some balancing (20...50mA), but the cells should be in a similar state of charge when the packs are assembled.

To retrieve the cells, carefully disassemble the Tattu battery packs.
The cells are unprotected so make sure you don't short-circuit the contacts while soldering.
The bare cells should look like this:

<table align="center">
  <tr>
    <td align="center">
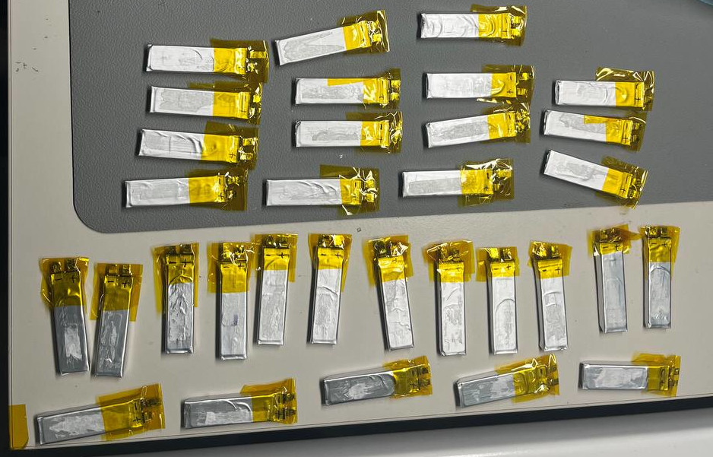
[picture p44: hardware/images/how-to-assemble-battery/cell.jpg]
      <br/>
    </td>
  </tr>
</table>

## Prepare Cell Adapter and Cell Protection PCBs
The [cell-adapter PCBs](electronics/gerbers/cell-adapter) should have two press-fit inserts for the zero mating height balancing connectors.
These connectors serve as contacts for balancing and for mechanical alignment during assembly.
Make sure the press fit inserts are in place and hold firmly in the PCB.
If the press fit is too loose and the inserts fall out, it will be very difficult to replace them later.
If you find the inserts too loose, apply a tiny bit of solder to the press fit hole to make the press fit tighter.
You can test with the cell protection PCBs (see below) if the alignment pins and press fit inserts fit.

<table align="center">
  <tr>
    <td align="center">
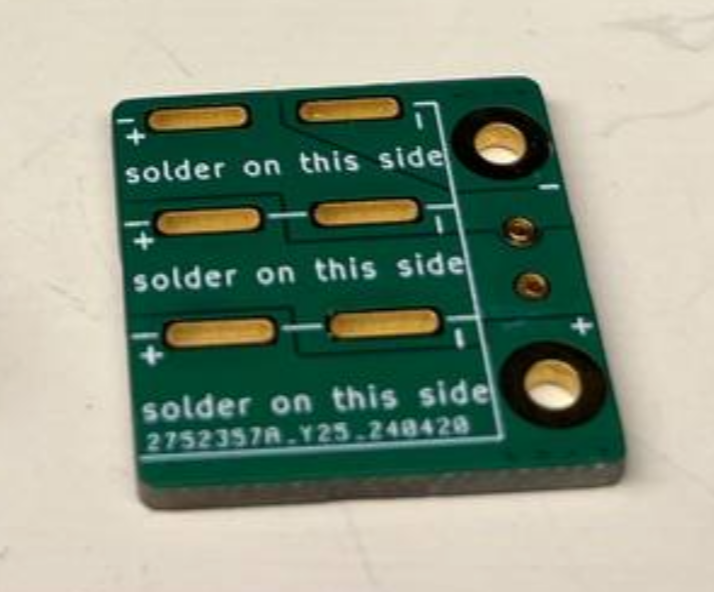
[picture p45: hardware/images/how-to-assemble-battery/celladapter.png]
      <br/>
    </td>
    <td align="center">
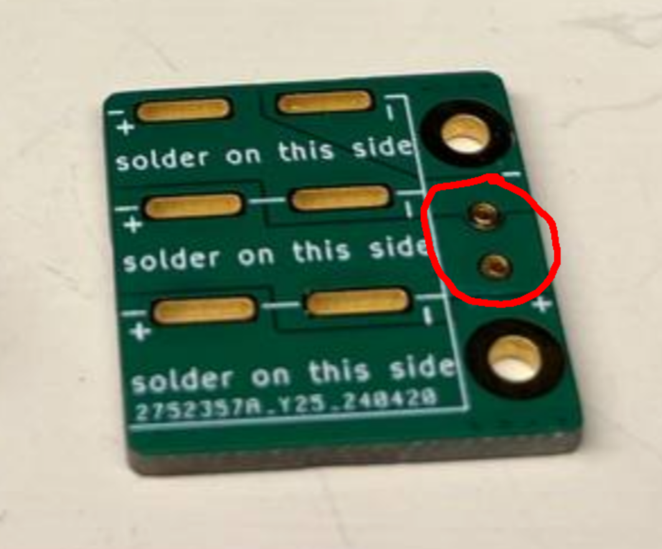
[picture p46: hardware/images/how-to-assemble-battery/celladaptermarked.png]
      <br/>
    </td>
  </tr>
</table>

If not already done, solder the thermistors to the [cell-protection PCBs](electronics/gerbers/cell-protection).
Make sure the alignment pins mate with the cell-adapter PCBs.
<table align="center">
  <tr>
    <td align="center">
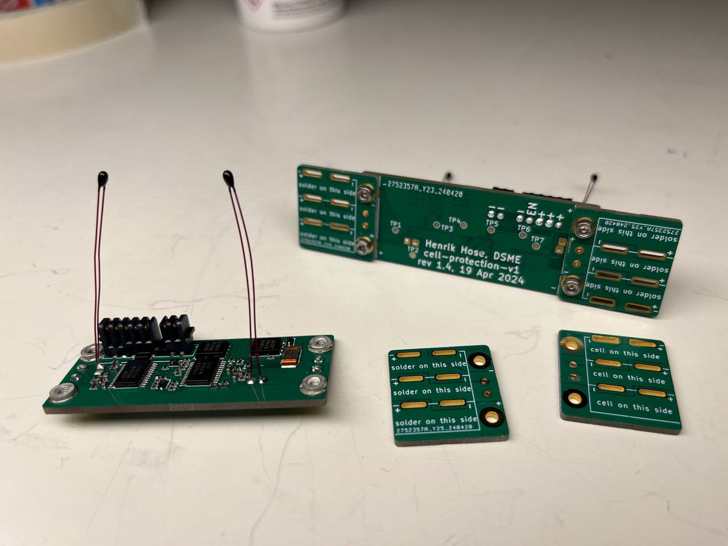
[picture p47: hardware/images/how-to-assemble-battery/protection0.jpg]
      <br/>
    </td>
    <td align="center">
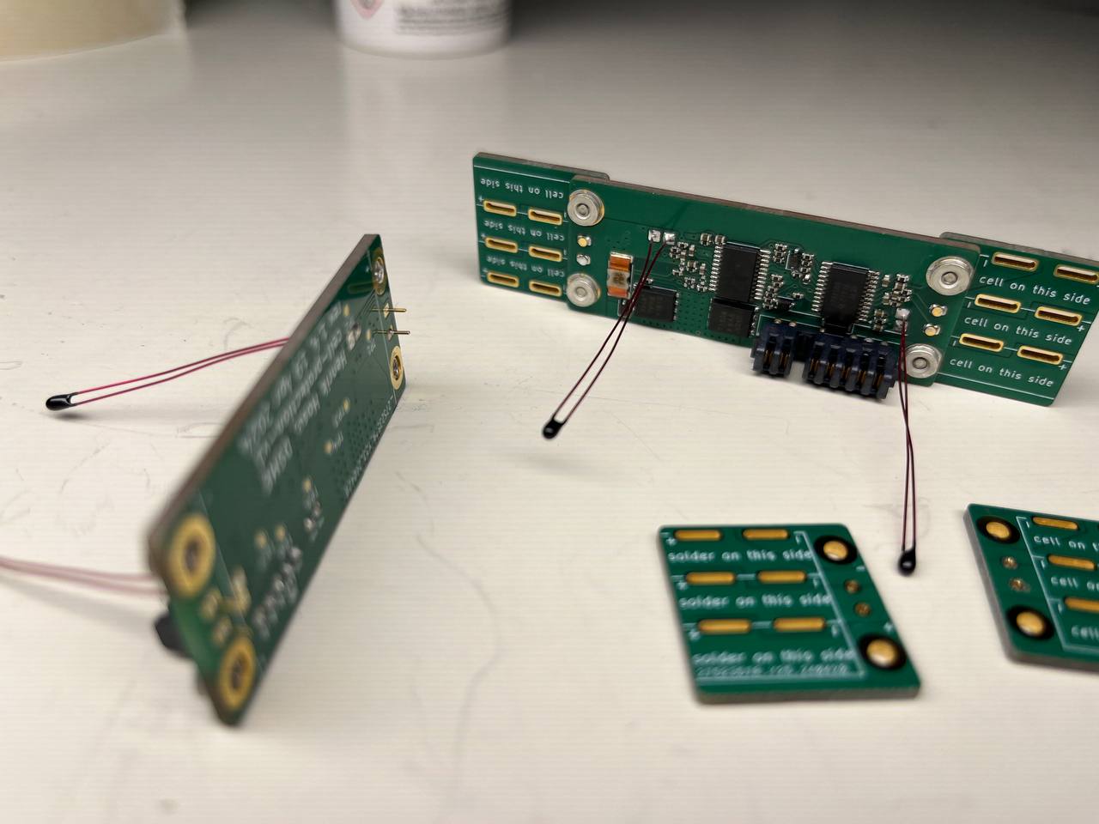
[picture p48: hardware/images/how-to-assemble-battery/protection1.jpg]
      <br/>
    </td>
    <td align="center">
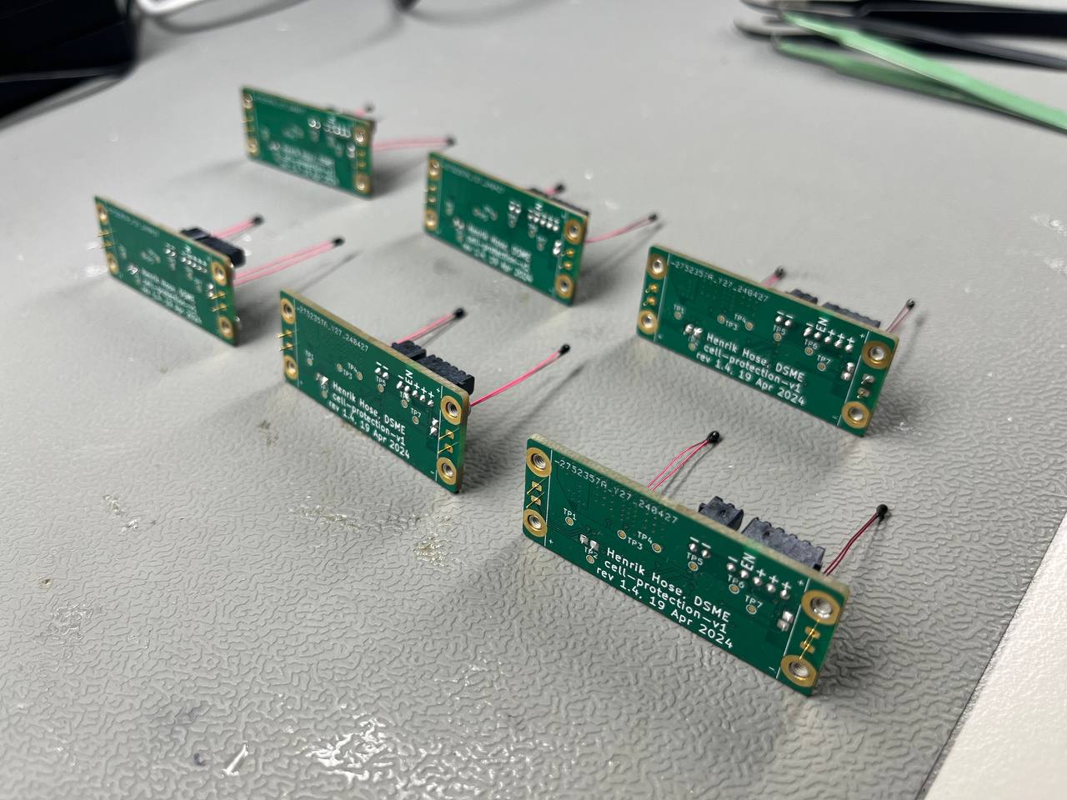
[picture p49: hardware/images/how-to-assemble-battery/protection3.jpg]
      <br/>
    </td>
    <td align="center">
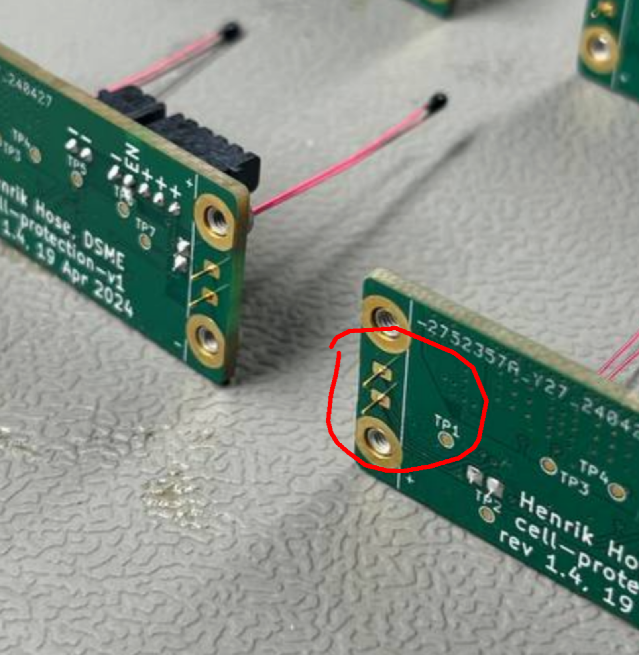
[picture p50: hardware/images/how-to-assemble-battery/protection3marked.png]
      <br/>
    </td>
  </tr>
</table>

## Solder Cells to Adapter
Solder three cells to the [cell-adapter PCBs](electronics/gerbers/cell-adapter).
Make sure to put the cells on the correct side (marked on the silk screen of the PCB with "cell on this side") and pay attention to the polarity as marked on the silk screen.
The cells should be perpendicular to the cell adapter PCB, avoid too much skew as this will put tension on the cell tabs when the final pack is inside the robot.

<table align="center">
  <tr>
    <td align="center">
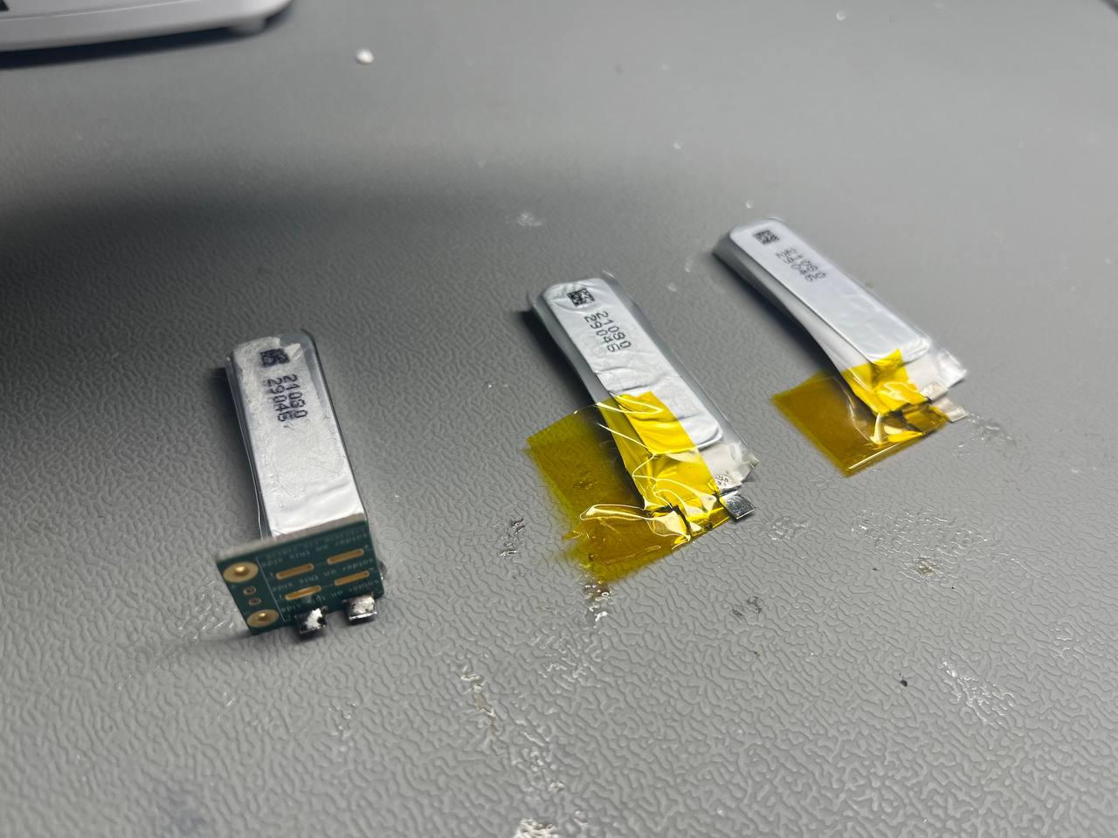
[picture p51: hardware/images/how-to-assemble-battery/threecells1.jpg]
      <br/>
    </td>
    <td align="center">
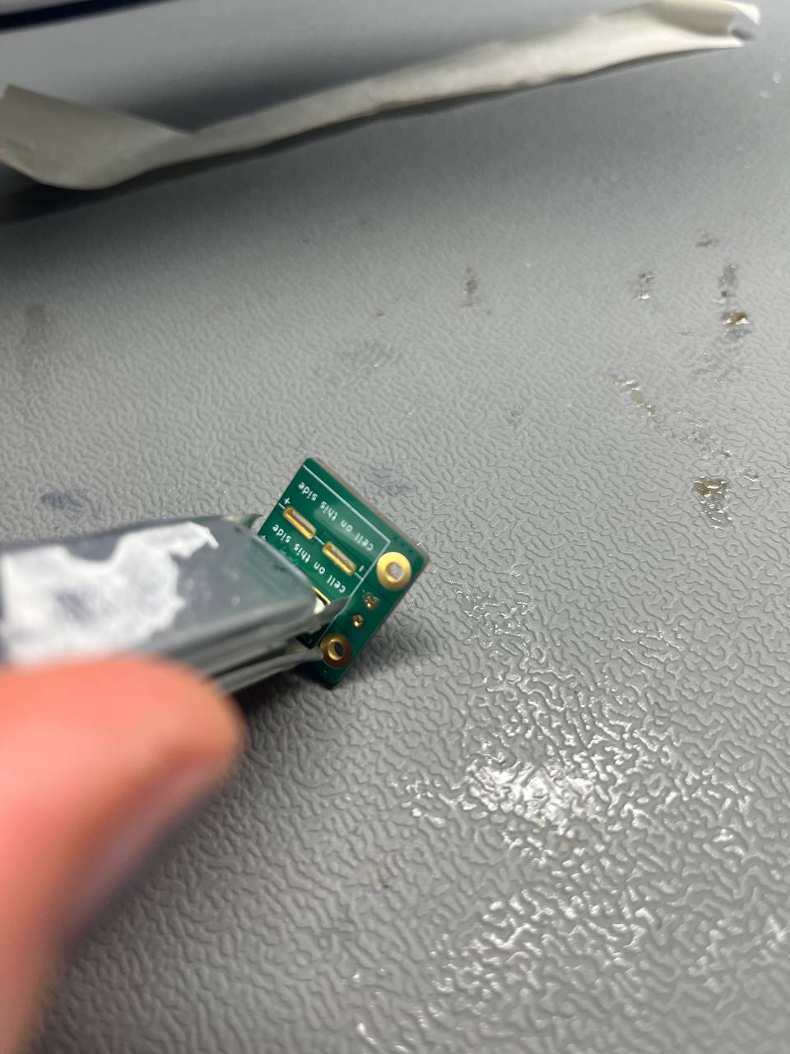
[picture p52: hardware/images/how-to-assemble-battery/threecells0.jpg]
      <br/>
    </td>
    <td align="center">
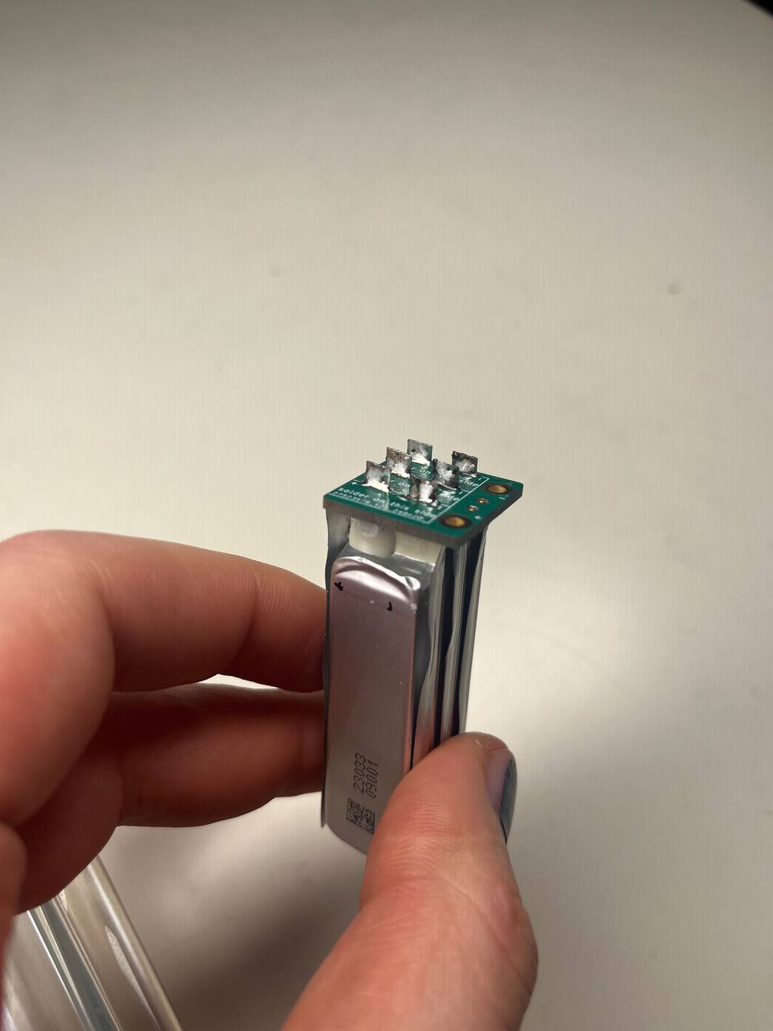
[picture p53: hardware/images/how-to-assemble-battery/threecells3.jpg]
      <br/>
    </td>
    <td align="center">
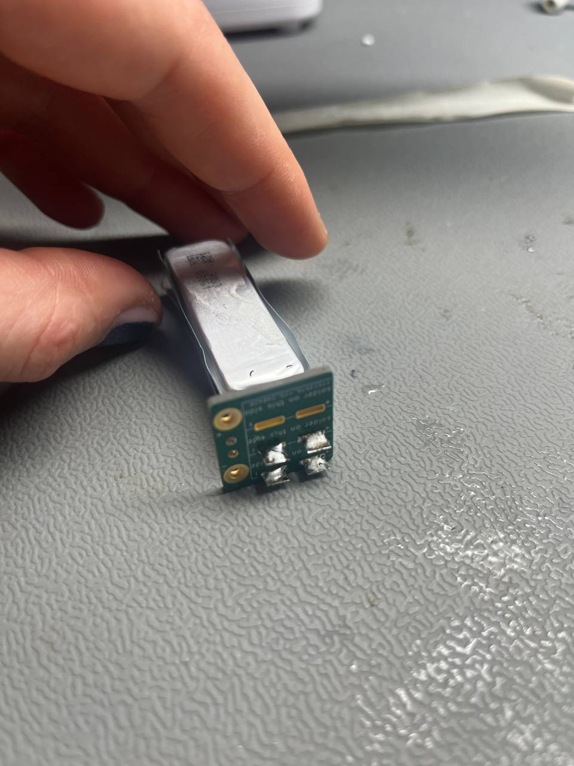
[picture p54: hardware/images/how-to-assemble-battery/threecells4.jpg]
      <br/>
    </td>
    <td align="center">
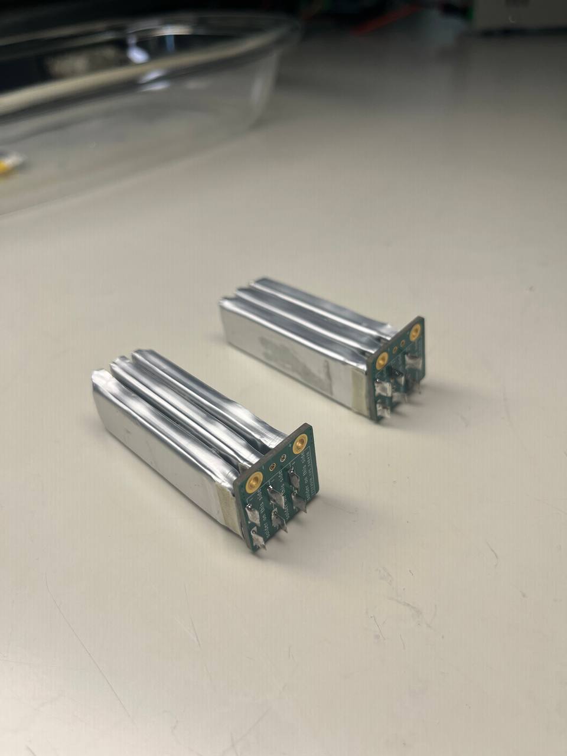
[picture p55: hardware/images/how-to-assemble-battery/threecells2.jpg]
      <br/>
    </td>
  </tr>
</table>

You may want to cover the bare cell contacts with tape now, e.g., 3M ET 1339 tape.
<table align="center">
  <tr>
    <td align="center">
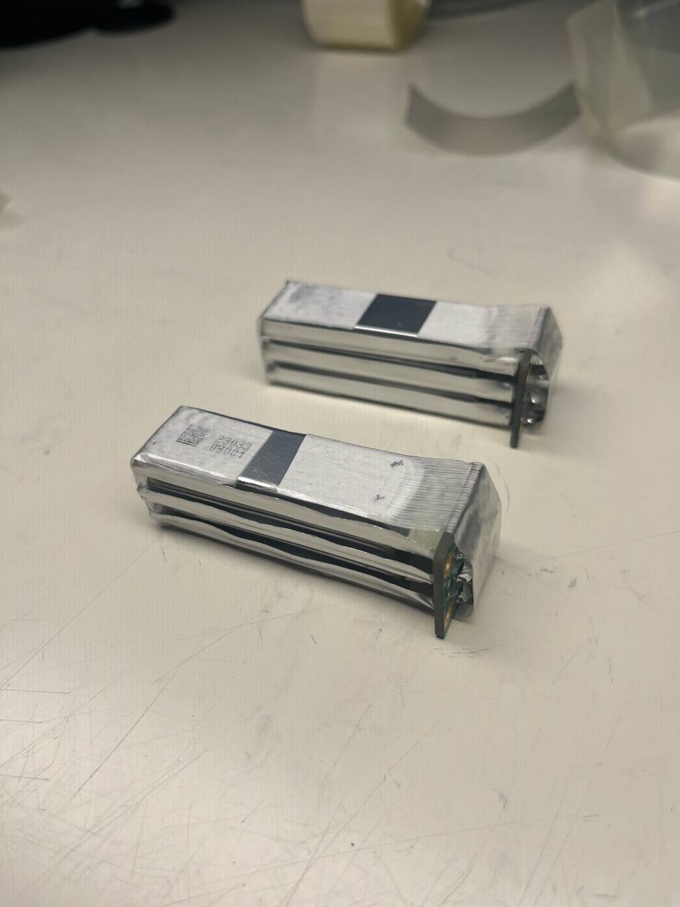
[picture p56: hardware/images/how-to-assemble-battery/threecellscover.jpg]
      <br/>
    </td>
  </tr>
</table>

## Assemble the Pack
Have 4x DIN912 M2x4mm socket head screw and 4x washer to hand.
Carefully align the cell adapter with its three cells to the cell protection PCB using the two pins and press-fit inserts.
When the cells are well aligned, carefully fasten with washer and screw without short-circuiting anywhere.
If your hands shake, use tape to temporarily mask contacts.
Repeat on the other side.
Tighten both M2 screws per cell adapter firmly as they make the contact that carries the main battery current.

<table align="center">
  <tr>
    <td align="center">
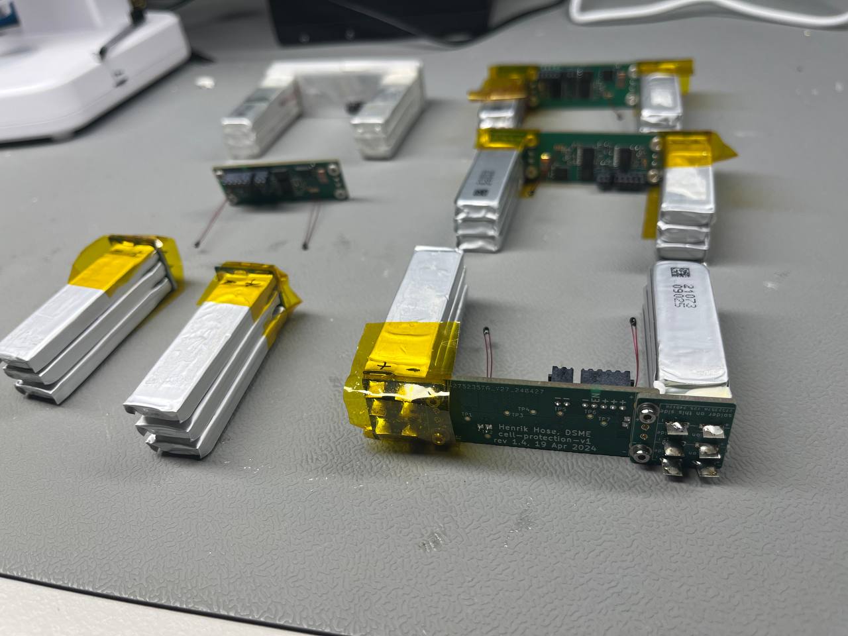
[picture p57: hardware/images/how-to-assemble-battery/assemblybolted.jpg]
      <br/>
    </td>
    <td align="center">
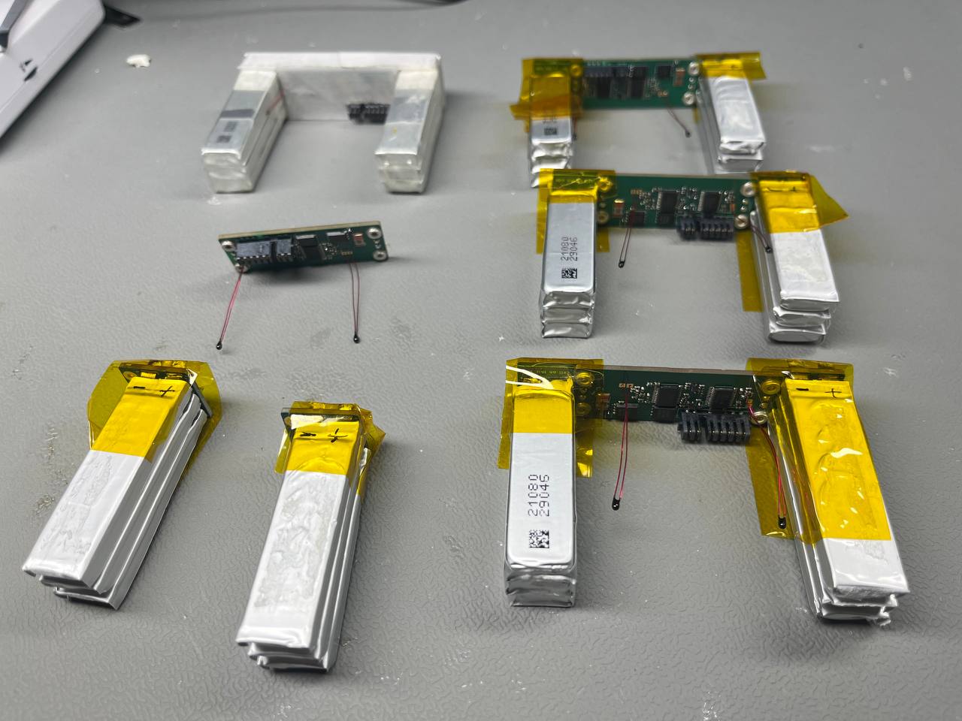
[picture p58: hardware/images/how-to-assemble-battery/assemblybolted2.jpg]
      <br/>
    </td>
  </tr>
</table>

Once bolted down, use 3M ET 1339 tape if you didn't previously, to cover the cell taps and wrap around the three pack of cells right below the cell adapter.
Then, use electrical grade silicone, e.g., Chip Quik EGS10C­20G, to generously back-fill any cavities between cells (marked B below) and cell-adapter and between cell adapter and soldered taps (marked A below).
The purpose of the silicone is to prevent the cell taps from crushing or buckling under mechanical pressure.
<table align="center">
  <tr>
    <td align="center">
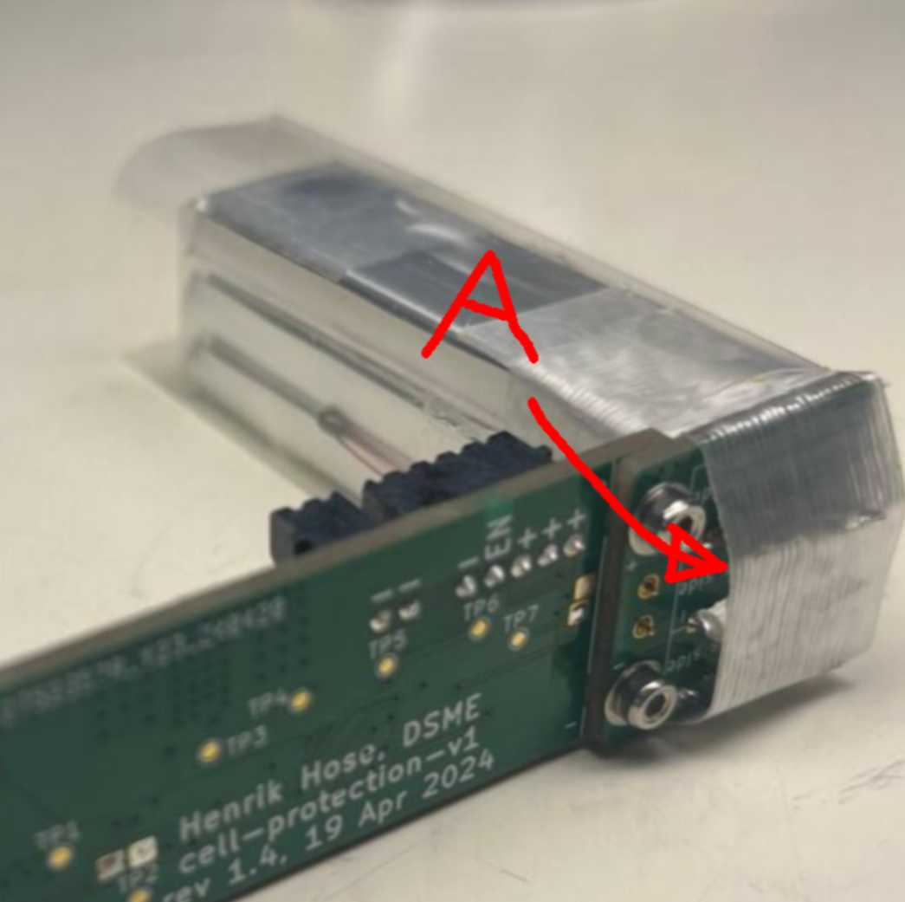
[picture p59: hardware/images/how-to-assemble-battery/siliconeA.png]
      <br/>
    </td>
    <td align="center">
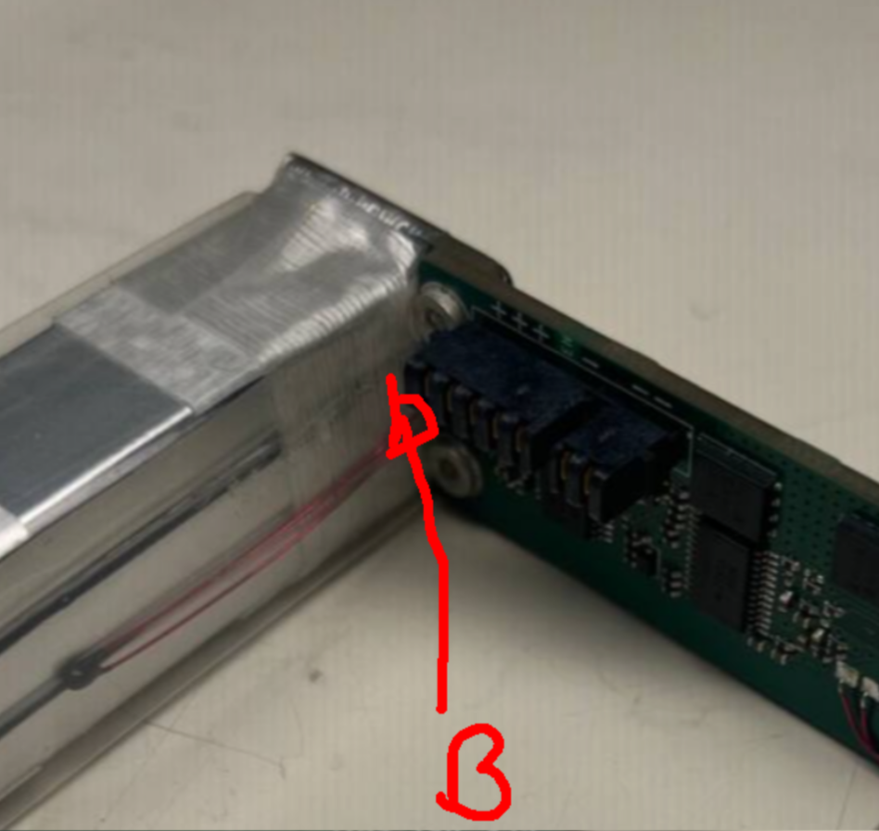
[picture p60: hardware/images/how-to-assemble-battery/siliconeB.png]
      <br/>
    </td>
  </tr>
</table>

Cut off pieces of shrink wrap to cover the cells.
These should be about 5-10mm longer than the cells. 
Use plastic tweezers or your fingers to bend the thermistors flat against the cells on each side and pull the shrink wrap over.
Then use a hot air gun to carefully shrink in the cells.
<table align="center">
  <tr>
    <td align="center">
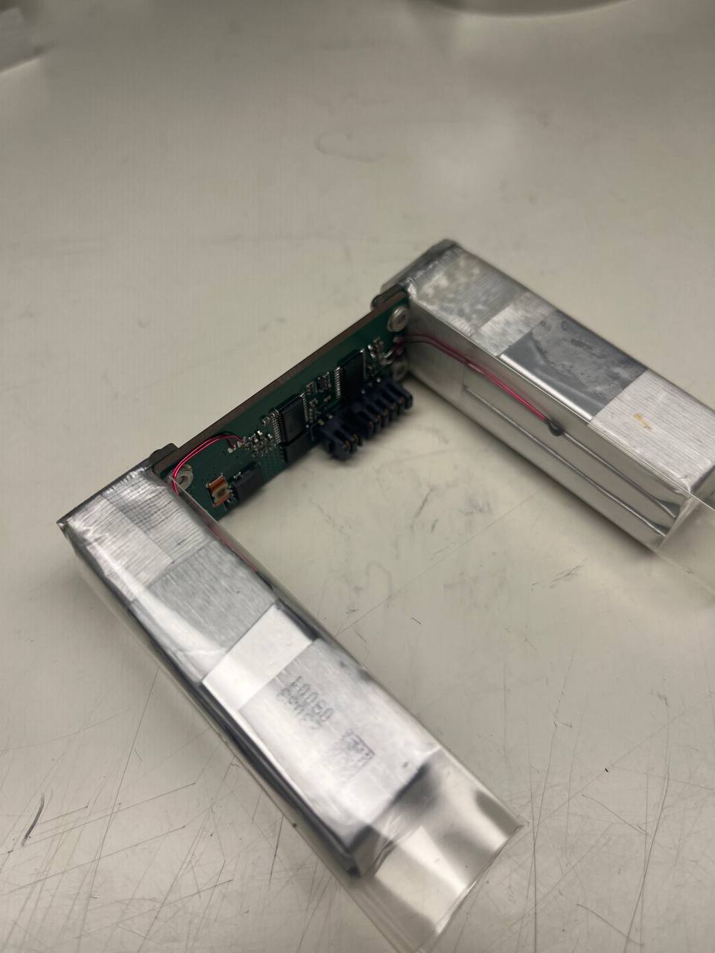
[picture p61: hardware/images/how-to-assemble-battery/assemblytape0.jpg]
      <br/>
    </td>
    <td align="center">
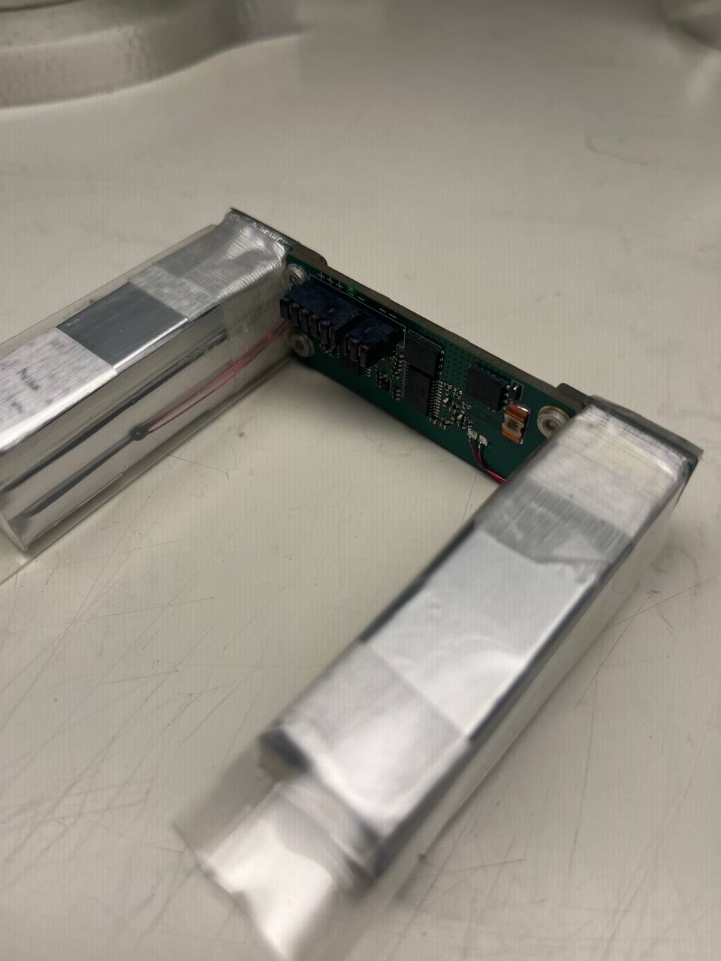
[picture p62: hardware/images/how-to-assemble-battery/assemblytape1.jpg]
      <br/>
    </td>
  </tr>
</table>

Finally, cover in 3D printed housing and wrap with 3M ET 1339 tape to secure the lid on the housing.
<table align="center">
  <tr>
    <td align="center">
      <br/>
    </td>
    <td align="center">
      <br/>
    </td>
  </tr>
</table>

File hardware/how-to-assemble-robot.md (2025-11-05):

# Assembling the Mini Wheelbot

## Motors
To assemble the motors, first the precrimped JST-XH (2 in) cables are cut to length, soldered to the motors and inserted into the JST-XH 3 pin plug housings.

<table align="center">
  <tr>
    <td align="center">
      <br/>
    </td>
    <td align="center">
      <br/>
    </td>
  </tr>
</table>

## Encoder magnets

The magnets are press-fitted into the 3D-printed parts.

<p align="center">
  
</p>

## Interior body - 3D printed parts

The two flex PCBs that hold the IMUs are glued to the interior body parts as shown below.

<table align="center">
  <tr>
    <td align="center">
      <br/>
    </td>
    <td align="center">
      <br/>
    </td>
  </tr>
</table>

Four M2.5 x 4mm threaded 3D print inserts are installed at the shown positions. They are used to install the CM4 and to fix the robots aluminium body.

<p align="center">
  
</p>

Two M2x3mm threaded 3D print inserts are installed at the shown positions. They are used to install the motor controllers.

<table align="center">
  <tr>
    <td align="center">
      <br/>
    </td>
    <td align="center">
      <br/>
    </td>
  </tr>
</table>

Three M2.5 x 4mm threaded 3D print inserts are installed at the shown positions. They are used to install the CM4 and the motor connector cable.

<p align="center">
  
</p>

## Motor connector cable

The precrimped JST-XH (4 in) cables are cut to length, soldered to the PCB and inserted into the JST-XH 3 pin plug housing. The cables are shielded using shielding copper tape.
The final motor connector cable is shown below.

<table align="center">
  <tr>
    <td align="center">
      <br/>
    </td>
    <td align="center">
      <br/>
    </td>
  </tr>
</table>

## Encoder cables

For both lengths, the six precrimped JST-GH cables are inserted into the JST-GH 6 pin plug housings. Then, the cables are twisted as shown below.

<p align="center">
  <br/>
</p>

## Installing the motor controllers

The two motor controllers are inserted into the interior body part and fastened using one M2 x 4mm socket head screw each.

<table align="center">
  <tr>
    <td align="center">
      <br/>
    </td>
    <td align="center">
      <br/>
    </td>
    <td align="center">
      <br/>
    </td>
    <td align="center">
      <br/>
    </td>
  </tr>
</table>

## Installing the power distribution board

The motor controllers are connected to the power distribution board as shown below.

<table align="center">
  <tr>
    <td align="center">
      <br/>
    </td>
    <td align="center">
      <br/>
    </td>
    <td align="center">
      <br/>
    </td>
    <td align="center">
      <br/>
    </td>
    <td align="center">
      <br/>
    </td>
  </tr>
</table>

Then, the other interior body part is installed using two M3 x 8mm and one M2 x 8mm socket head screw.

<table align="center">
  <tr>
    <td align="center">
      <br/>
    </td>
    <td align="center">
      <br/>
    </td>
    <td align="center">
      <br/>
    </td>
    <td align="center">
      <br/>
    </td>
    <td align="center">
      <br/>
    </td>
  </tr>
</table>

## Installing the motor connector cable

The motor connector cable is plugged into one of the motor controllers as shown below.

<p align="center">
  <br/>
</p>

The cable is routed around the outside of the interior body. The copper shielding has to be positioned as shown below to shield the Pi CM4 from the motor connector cable.

<p align="center">
  <br/>
</p>

The PCB at the end of the cable is installed using a M2.5 x 4mm socket head screw.

<p align="center">
  <br/>
</p>

## Installing the CM4 carrier board and the Pi CM4

The two flex PCBs are connected to the carrier board and the carrier board is connected to the power distribution board as shown below.

<table align="center">
  <tr>
    <td align="center">
      <br/>
    </td>
    <td align="center">
      <br/>
    </td>
  </tr>
</table>

The carrier board is fastened using four M2.5 x 10mm set screws and four M2.5 nuts (flat).

<table align="center">
  <tr>
    <td align="center">
      <br/>
    </td>
    <td align="center">
      <br/>
    </td>
  </tr>
</table>

The Pi CM4 is connected to the carrier board and fastened using four M2.5 nuts (flat).

<p align="center">
  <br/>
</p>

## Installing the encoder cables

The encoder cables are connected to the motor controllers as shown below.

<table align="center">
  <tr>
    <td align="center">
      <br/>
    </td>
    <td align="center">
      <br/>
    </td>
    <td align="center">
      <br/>
    </td>
  </tr>
</table>

## Installing the first motor

The wheel that is perpendicular to the Pi CM4 is installed before the interior is slid into the aluminium body. The motor cables are connected to the motor controller as shown below.

<table align="center">
  <tr>
    <td align="center">
      <br/>
    </td>
    <td align="center">
      <br/>
    </td>
    <td align="center">
      <br/>
    </td>
  </tr>
</table>

## Sliding the interior into the aluminium body

The interior is slid into the aluminium body as shown below. It is important to take care of the encoder cables and the motor connector cable next to the Pi CM4.

<table align="center">
  <tr>
    <td align="center">
      <br/>
    </td>
    <td align="center">
      <br/>
    </td>
    <td align="center">
      <br/>
    </td>
  </tr>
</table>

After the interior is fully slid in, pass the encoder cables through the corresponding holes.

<table align="center">
  <tr>
    <td align="center">
      <br/>
    </td>
    <td align="center">
      <br/>
  </tr>
</table>

## Fasten the first motor

The first motor is fastened to the aluminium body using three M3 x 6mm socket head screws.

<p align="center">
  <br/>
</p>

## Installing the second motor

The second motor is connected to the motor controller and fastened to the aluminium body using three M3 x 6mm socket head screws.

<table align="center">
  <tr>
    <td align="center">
      <br/>
    </td>
    <td align="center">
      <br/>
  </tr>
</table>

## Installing the encoder magnets

The two encoder magnets are pressed onto the axles of the wheels.

<table align="center">
  <tr>
    <td align="center">
      <br/>
    </td>
    <td align="center">
      <br/>
  </tr>
</table>

## Fastening the aluminium body

The interior is fastened to the aluminium body using two M2.5 x 6mm flat head screws and two M3 x 20mm flat head screws.

<table align="center">
  <tr>
    <td align="center">
      <br/>
    </td>
    <td align="center">
      <br/>
  </tr>
</table>

## Installing the encoders

The encoders are connected to the encoder cables and fastened using two M2.5 x 4mm socket head screws each.

<table align="center">
  <tr>
    <td align="center">
      <br/>
    </td>
    <td align="center">
      <br/>
  </tr>
</table>

## Installing the battery pack

The battery pack is slid into the robot, connecting it to the power distribution board.

<table align="center">
  <tr>
    <td align="center">
      <br/>
    </td>
    <td align="center">
      <br/>
  </tr>
</table>

## Fastening the lids

The lids are fastened using four M3 x 6mm socket head screws each. On the Pi CM4 side, it is important to take care of the motor connector cable and the encoder cable when fastening the lid. 

<table align="center">
  <tr>
    <td align="center">
      <br/>
    </td>
    <td align="center">
      <br/>
    </td>
    <td align="center">
      <br/>
    </td>
    <td align="center">
      <br/>
  </tr>
</table>

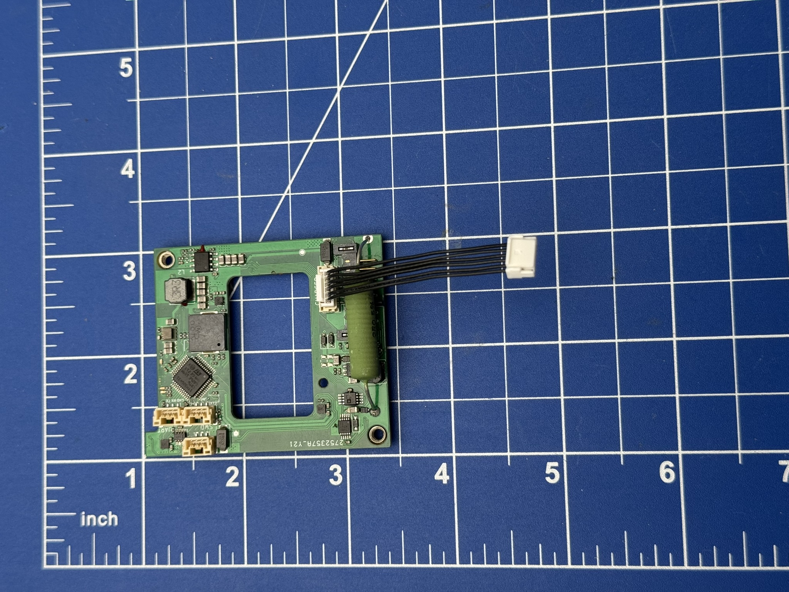
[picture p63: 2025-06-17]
hardware/images/how-to-assemble-robot/IMG_0328.JPEG

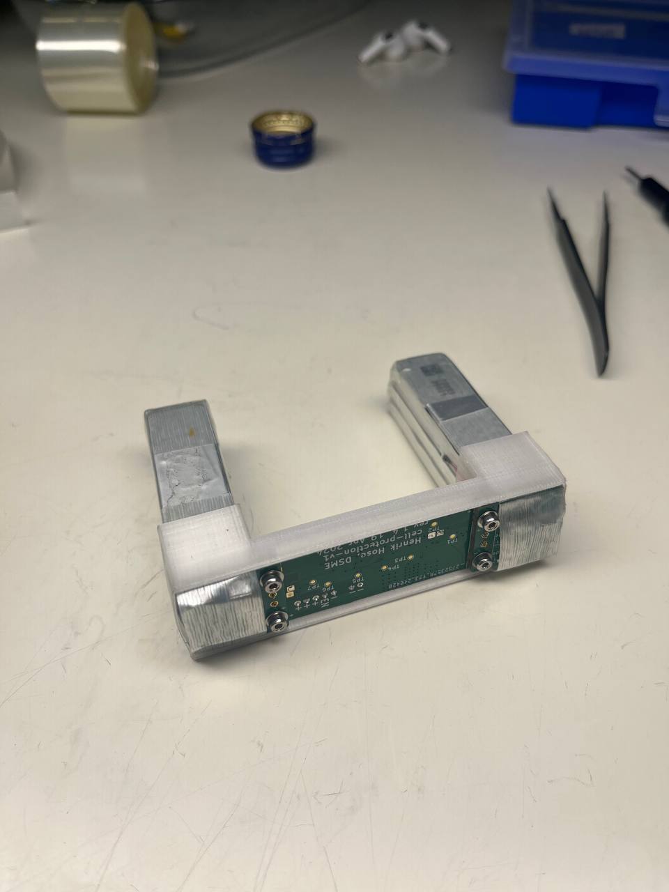
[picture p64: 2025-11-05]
hardware/images/how-to-assemble-battery/assemblytape2.jpg

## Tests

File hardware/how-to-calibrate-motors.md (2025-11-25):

# Motor Calibration Tutorial

This guide explains how the in `calibrateMotors.py` script in `/wheelbot-lib/scripts/micro-motor/` operates and what steps are performed during motor calibration. Follow these steps if you want to manually calibrate the motors.

---

## Reference: Motor Calibration Command Meanings

| Command | Example Frame | Description |
|---|---|---|
| `040#02` | `040#02` | Enable motor controller power |
| `040#01` | `040#01` | Disable motor controller power |
| `92` | `021#92`, `022#92` | **Disable cogging compensation** (required before recalibration) |
| `11` | `021#11`, `022#11` | Start encoder alignment routine |
| `12` | `021#12`, `022#12` | Start cogging compensation calibration |
| `46` | `021#46`, `022#46` | **Request special action status** (poll progress) |
| `91` | `021#91`, `022#91` | **Enable cogging compensation** after calibration |
| `23` | `021#23`, `022#23` | **Enable auto-reload** of cogging table on boot |
| `21` | `021#21`, `022#21` | **Save configuration to flash** |

## Setup

The can interface on the Mini Wheelbots CM4 is called motorCan.
Please first set the motor controller IDs via the given script.
```
setMotorControllerIDs.py
```

## 1. Connection to the Mini Wheelbot

For calibration, connect to the Mini Wheelbots CM4 via

```
ssh root@<robot-ip>
```

## 2. Enable Motor Controller Power

Calibration begins by powering the motor controllers:

```
cansend motorCan 040#02
```

---

## 3. Verify Motor Reachability

Send a CAN SYNC frame:

```
cansend motorCan 000#
```

Both motor controllers must respond with arbitration IDs:

```
081#
082#
```

Check this in a separate terminal on the CM4 via 

```
candump motorCan
```

If fewer than two replies appear, stop — check wiring, power, and CAN interface.

---

## 4. Disable Existing Cogging Compensation

Before recalibrating, previously stored cogging compensation must be turned off:

```
cansend motorCan 021#92
cansend motorCan 022#92
```

(`92` = disable cogging compensation)

---

## 5. Start Encoder Alignment

This routine aligns electrical and mechanical rotor positions:

```
cansend motorCan 021#11
cansend motorCan 022#11
```

Now wait **12 seconds** - the script does this automatically.
Motors will move! Ensure no obstacles and that the wheels can move freely.

---

## 6. Start Cogging Compensation Learning

This step measures cogging torque across the motor revolution:

```
cansend motorCan 021#12
cansend motorCan 022#12
```

This step can take several minutes.
Motors will move! Ensure no obstacles and that the wheels can move freely.

---

## 7. Monitor Calibration Progress

Periodically request calibration status:

```
cansend motorCan 021#46
cansend motorCan 022#46
```

Motors respond with:

```
091#01 XX YY
092#01 XX YY
```

Interpret `XX`:

| XX | Meaning |
|----|---|
| 06 | Calibration running |
| 07 | Calibration completed successfully |
| 08 | Calibration failed → stop |
| 09 | Calibration aborted → stop |

The script loops until **both motors return `07`**.

---

## 8. Apply and Store Calibration Results

After successful calibration:

```
cansend motorCan 021#91
cansend motorCan 022#91
```

Enables cogging compensation.

```
cansend motorCan 021#23
cansend motorCan 022#23
```

Enables auto-reload on startup.

```
cansend motorCan 021#21
cansend motorCan 022#21
```

Saves configuration to flash memory.

---

## 9. Disable Motor Controller Power

Calibration finishes by turning motors off:

```
cansend motorCan 040#01
```

This ensures safe shutdown.

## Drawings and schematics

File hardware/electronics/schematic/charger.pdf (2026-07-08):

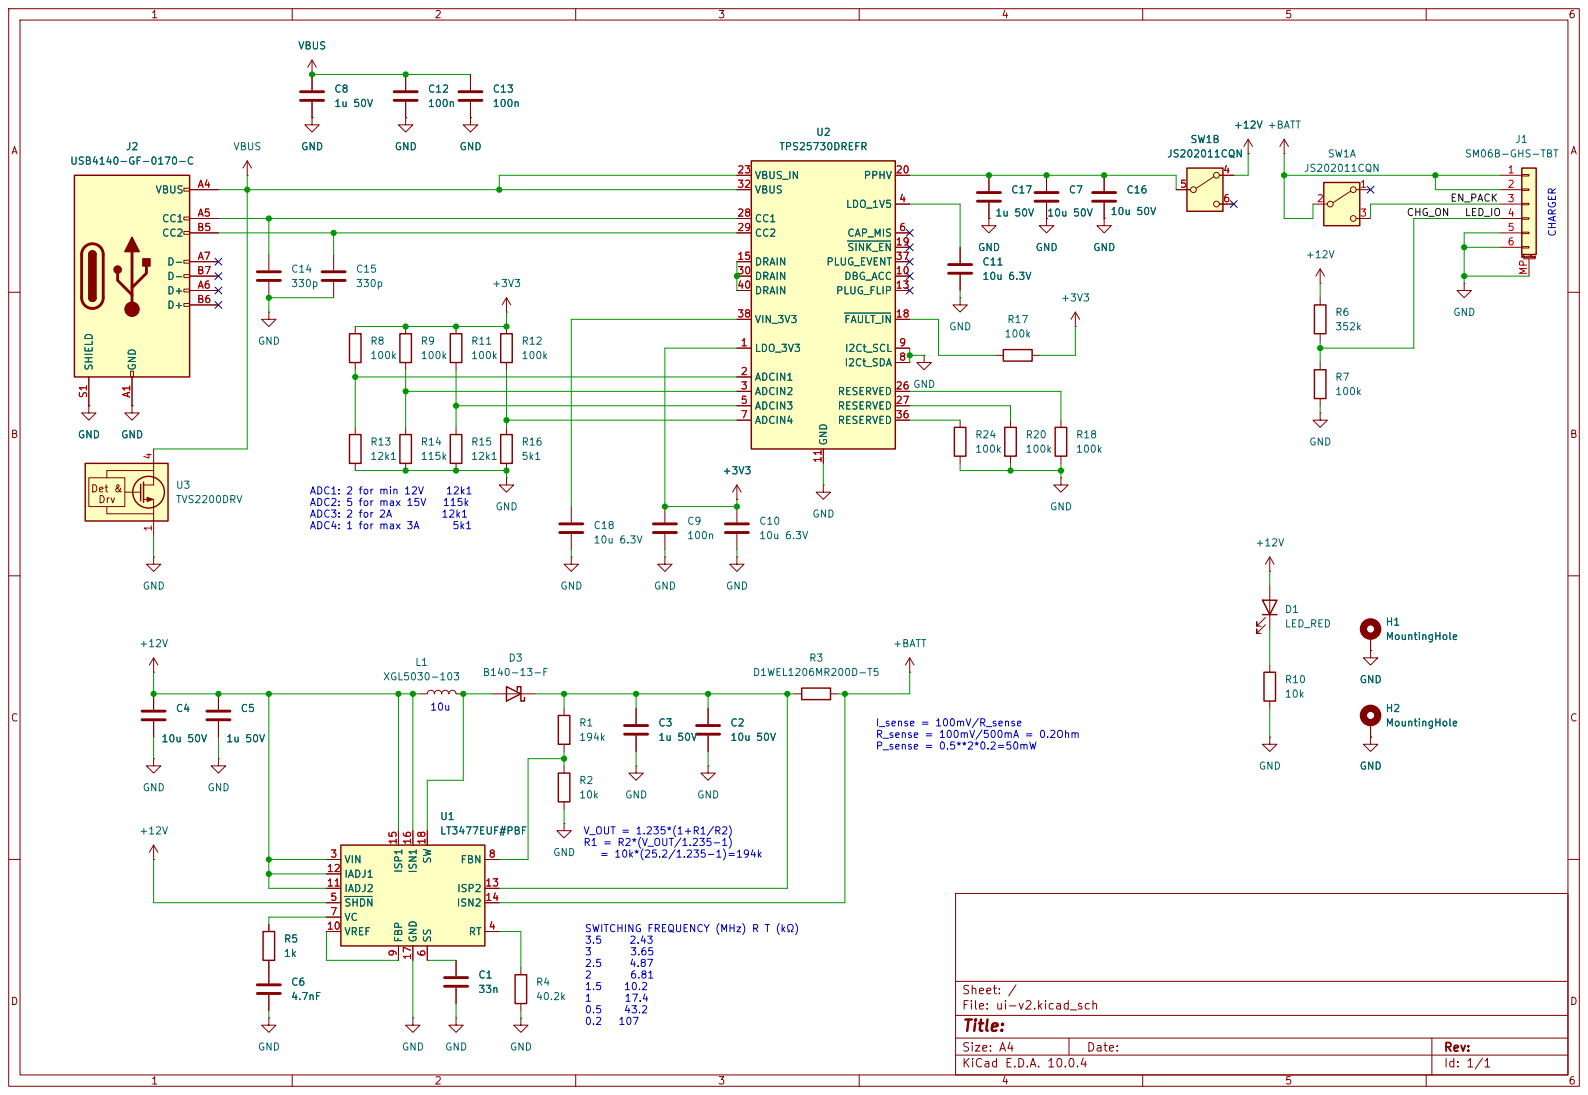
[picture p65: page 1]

100k R15 | ADCIN2 3

ADCIN4 7

Size: A4 | Rev:
KiCad E.D.A. 10.0.4 | Id: 1/1

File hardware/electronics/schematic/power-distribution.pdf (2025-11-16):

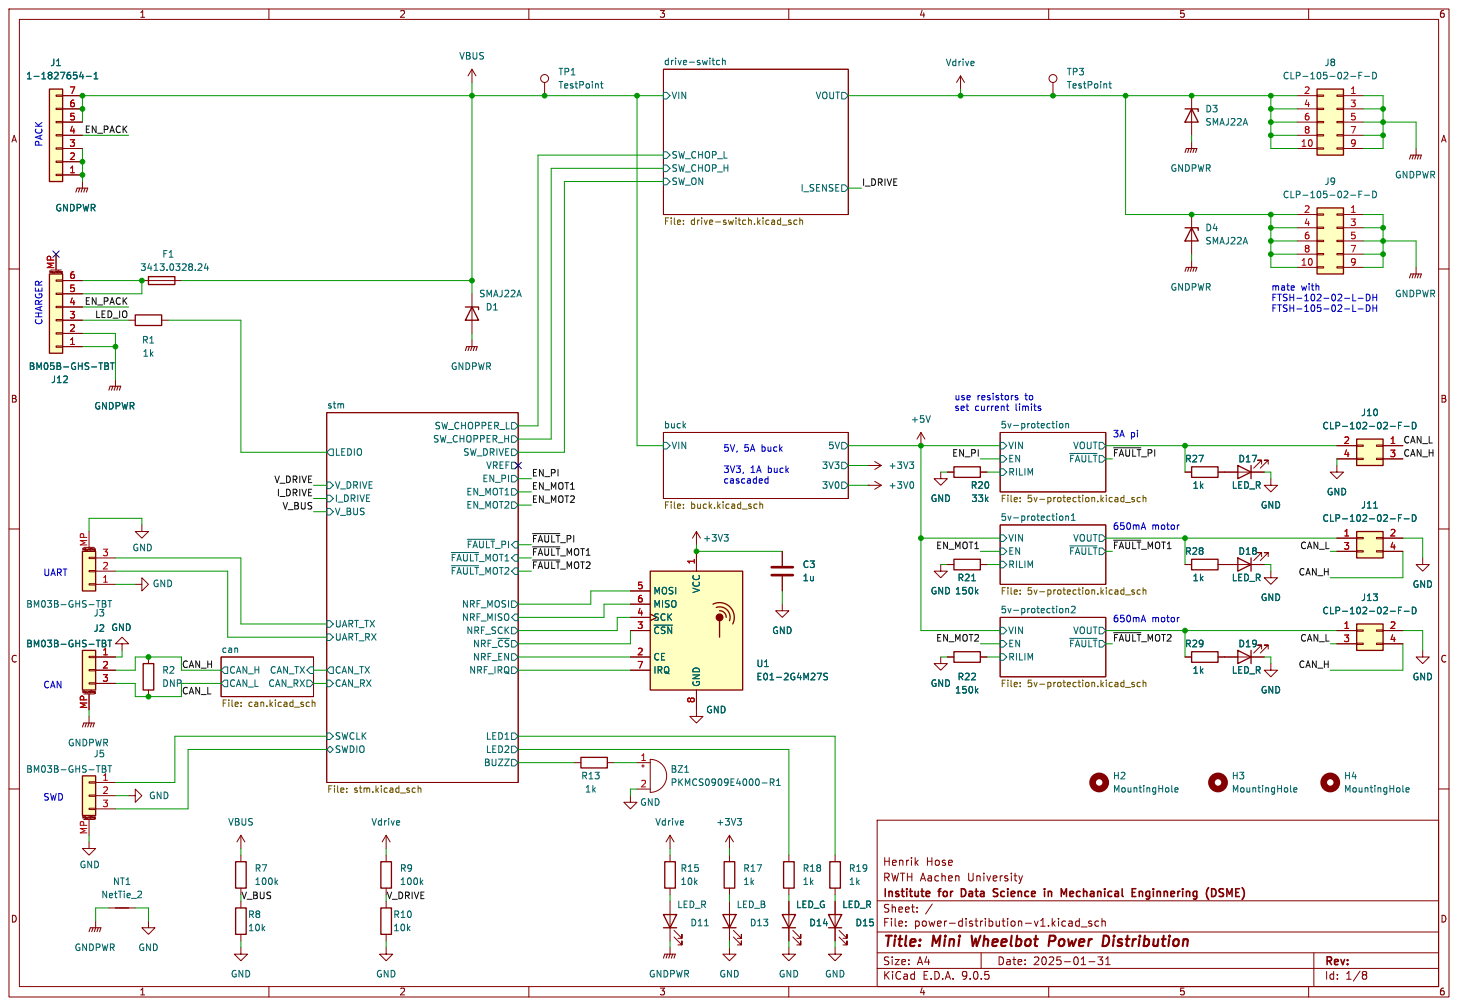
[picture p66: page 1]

set current limits SWD

U1E01-2G4M27S MOSI 5 MISO 6 SCK 4 ~{CSN} 3 CE 2

LED_R
Id: 1/8 Title: Mini Wheelbot Power Distribution

File: power-distribution-v1.kicad_sch Sheet: /

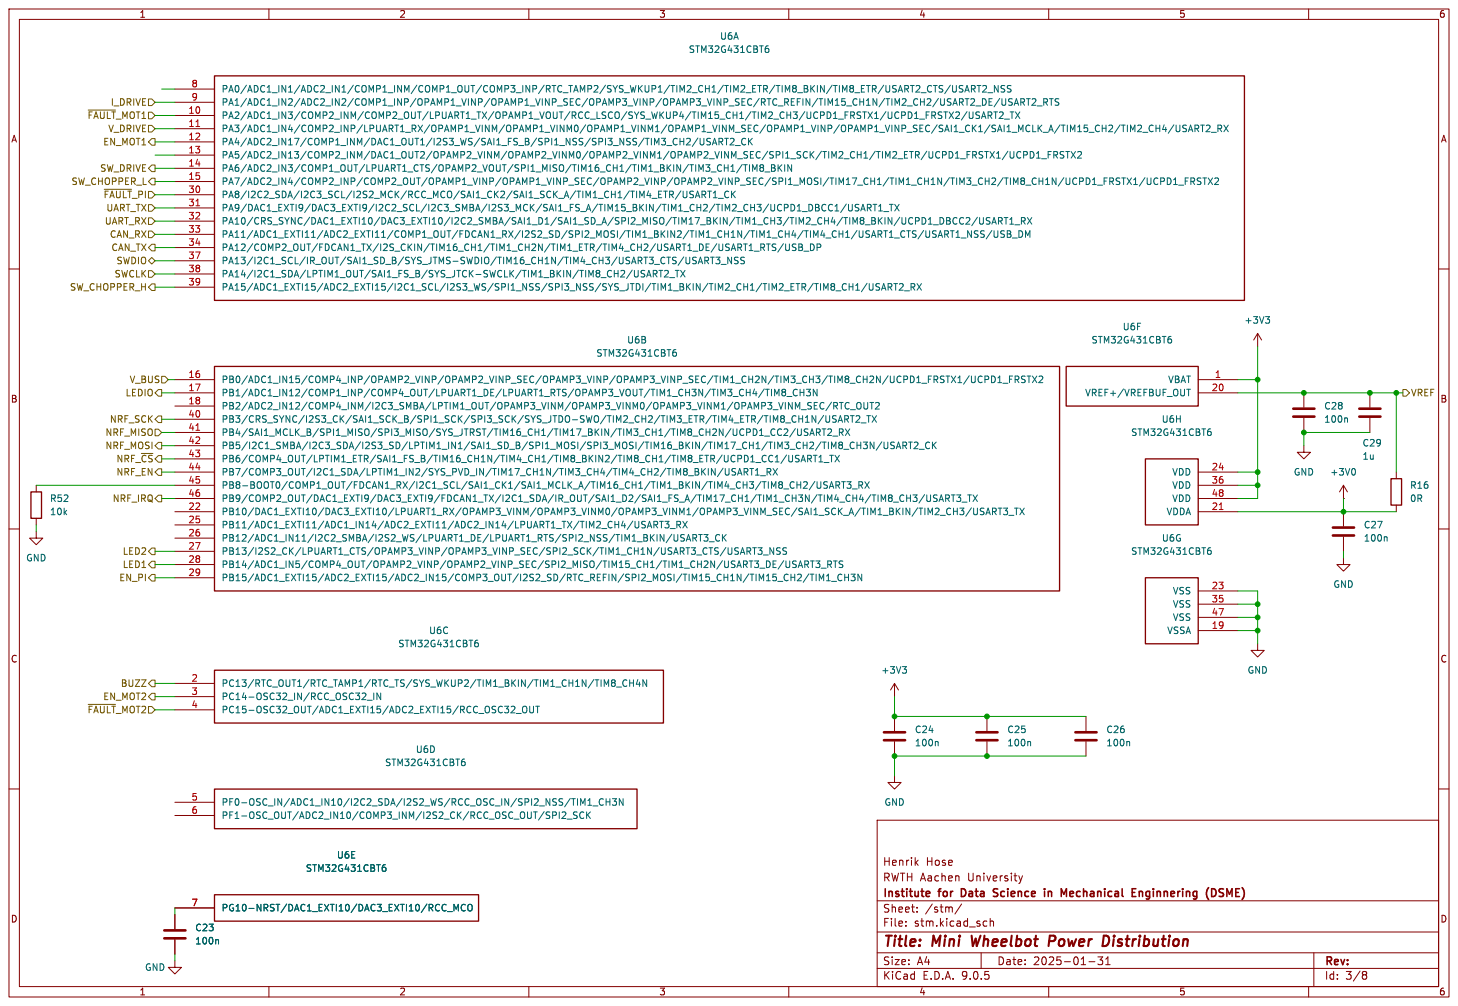
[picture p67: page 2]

File: stm.kicad_sch Sheet: /stm/
Id: 3/8 Title: Mini Wheelbot Power Distribution

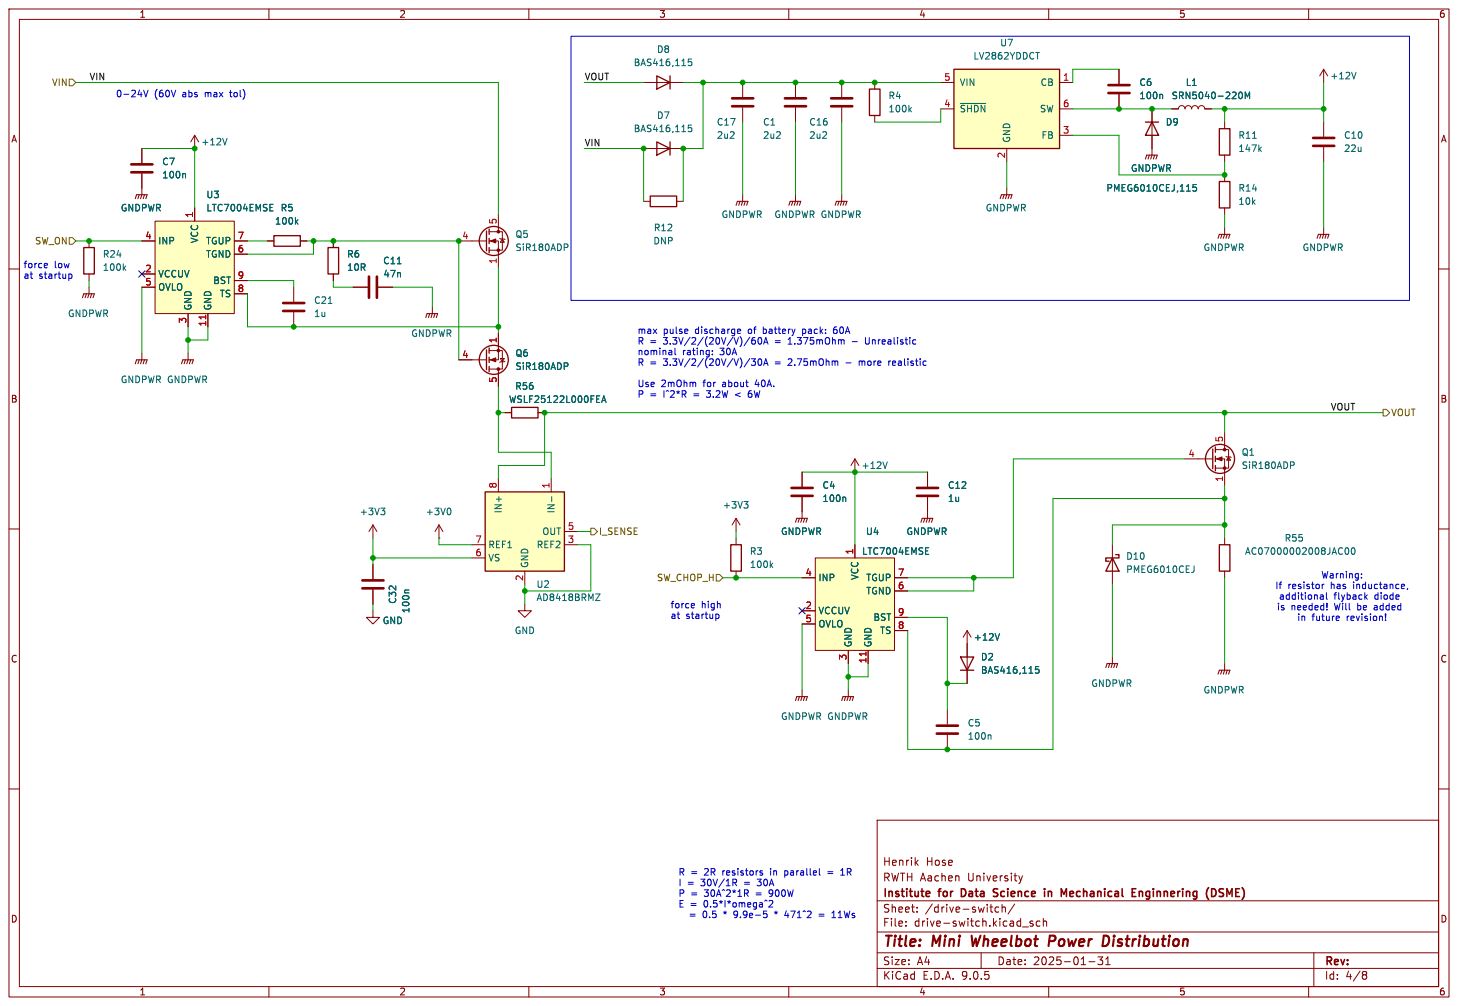
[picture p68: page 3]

1 GND 11 TGUP 7 TGND 6 BST 9 TS 8 U3

1 GND 11 TGUP 7 TGND 6 BST 9 TS 8 R5

2 IN- 1 OUT 5 REF2 3 U2AD8418BRMZ D2BAS416,115 GNDPWR GNDPWR

1 GND 11 TGUP 7 TGND 6 BST 9 TS 8 U4
LTC7004EMSE GNDPWR

1 GND 11 TGUP 7 TGND 6 BST 9 TS 8

is needed! Will be added
in future revision!

File: drive-switch.kicad_sch Sheet: /drive-switch/
Id: 4/8 Title: Mini Wheelbot Power Distribution

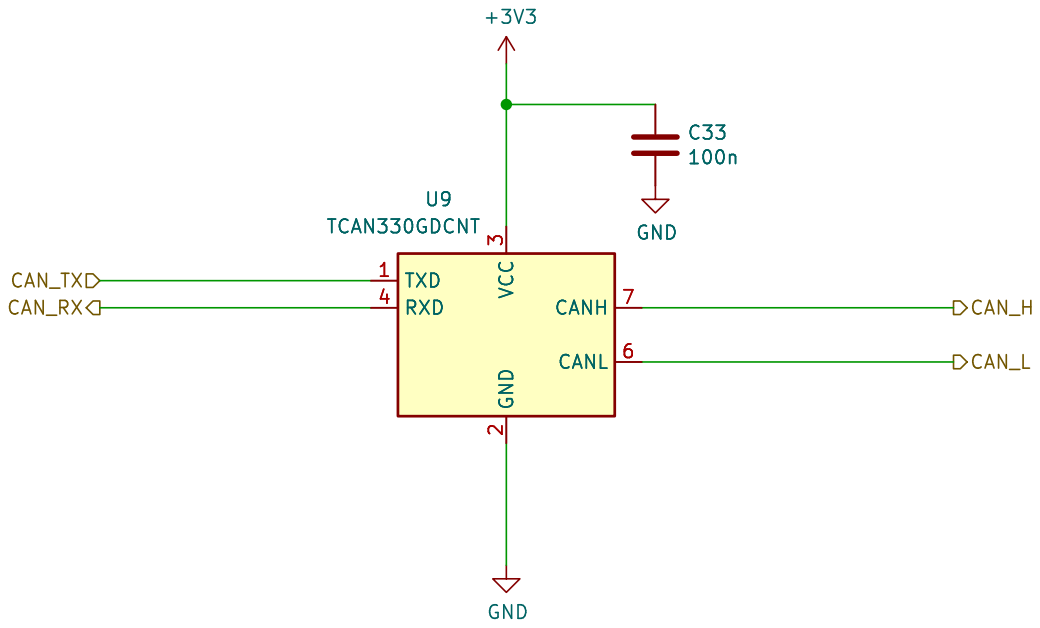
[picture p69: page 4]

File: can.kicad_sch Sheet: /can/
Id: 5/8 Title: Mini Wheelbot Power Distribution

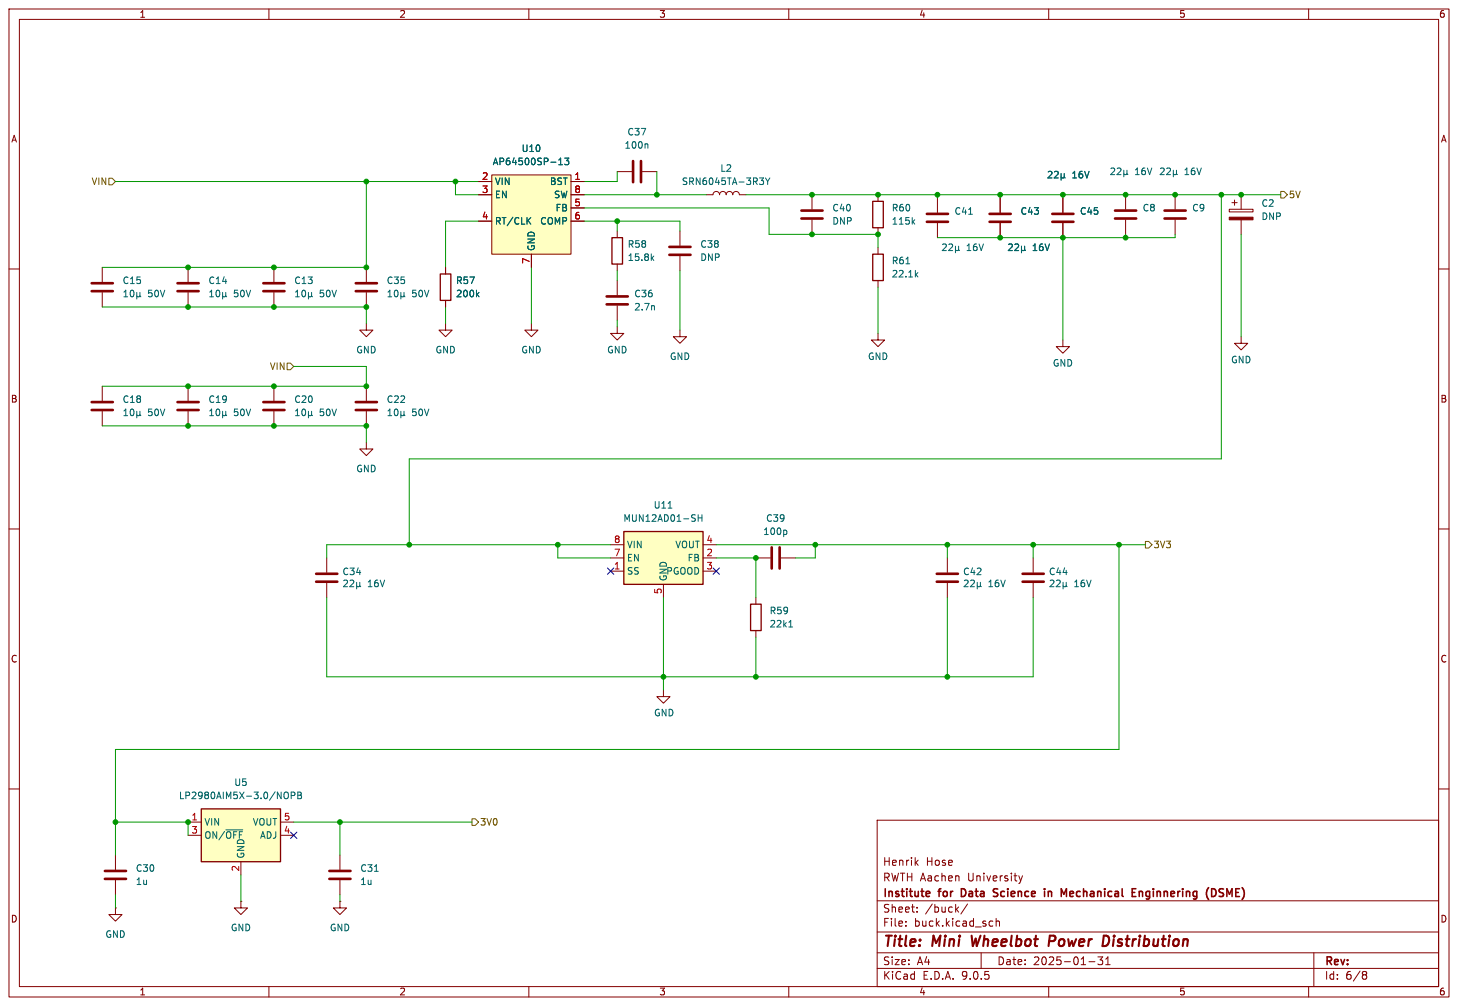
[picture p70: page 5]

7 BST 1 SW 8 FB 5 COMP 6 U10 AP64500SP-13 R57

7 BST 1 SW 8 FB 5 COMP 6 R57

5 VOUT 4 FB 2 PGOOD 3 U11 MUN12AD01-SH

File: buck.kicad_sch Sheet: /buck/
Id: 6/8 Title: Mini Wheelbot Power Distribution

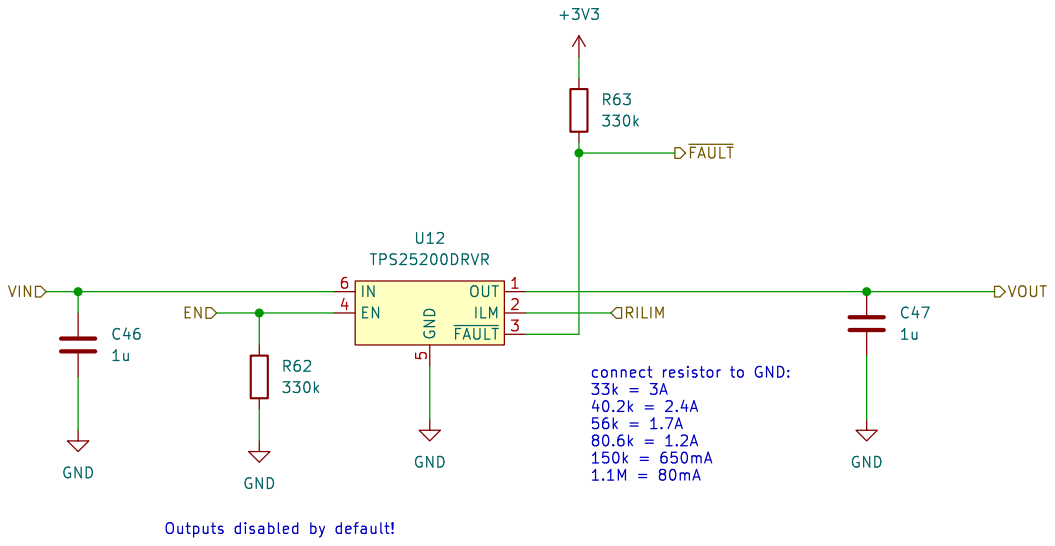
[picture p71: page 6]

File: 5v-protection.kicad_sch Sheet: /5v-protection/
Id: 7/8 Title: Mini Wheelbot Power Distribution

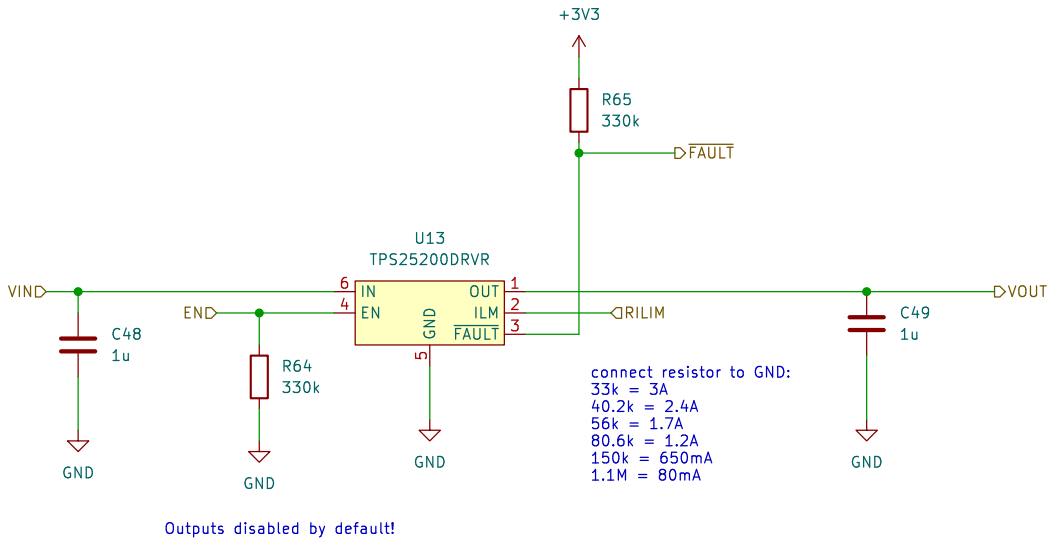
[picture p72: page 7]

File: 5v-protection.kicad_sch Sheet: /5v-protection1/
Id: 8/8 Title: Mini Wheelbot Power Distribution

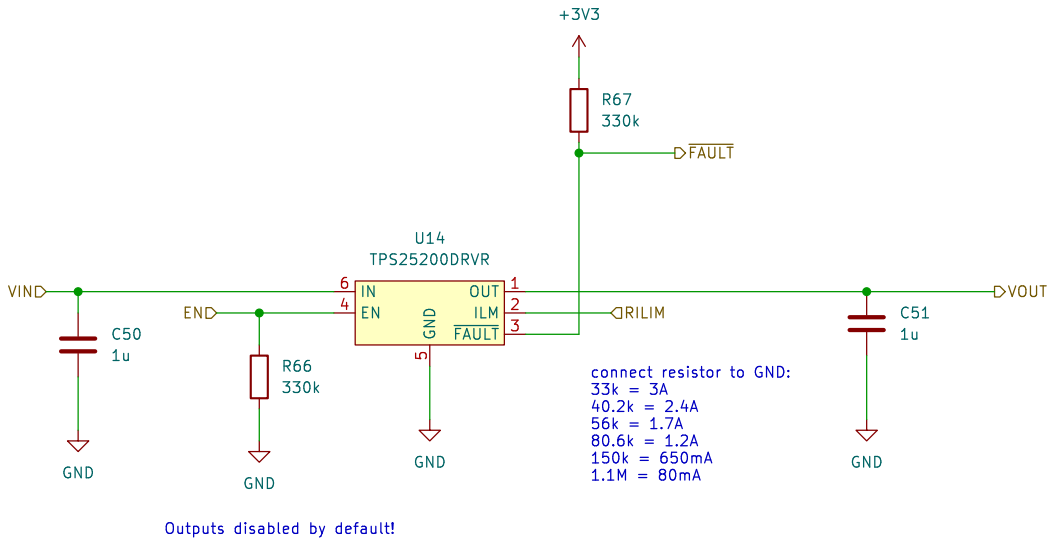
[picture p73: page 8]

File: 5v-protection.kicad_sch Sheet: /5v-protection2/
Id: 9/8 Title: Mini Wheelbot Power Distribution

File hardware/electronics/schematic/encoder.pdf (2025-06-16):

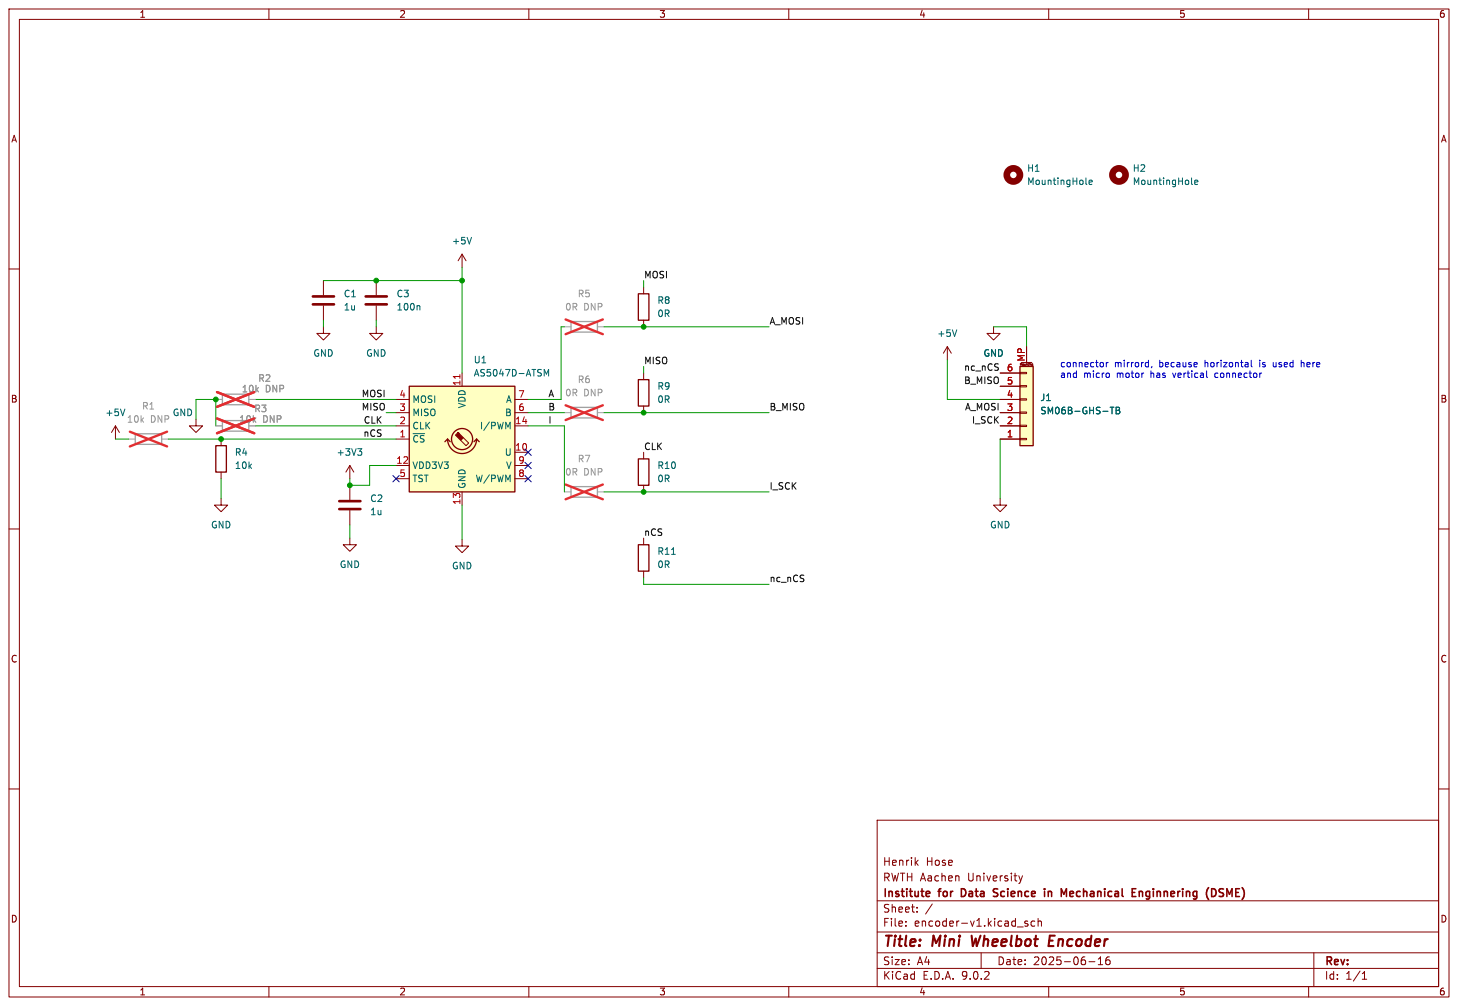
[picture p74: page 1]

Id: 1/1 Title: Mini Wheelbot Encoder File: encoder-v1.kicad_sch Sheet: /

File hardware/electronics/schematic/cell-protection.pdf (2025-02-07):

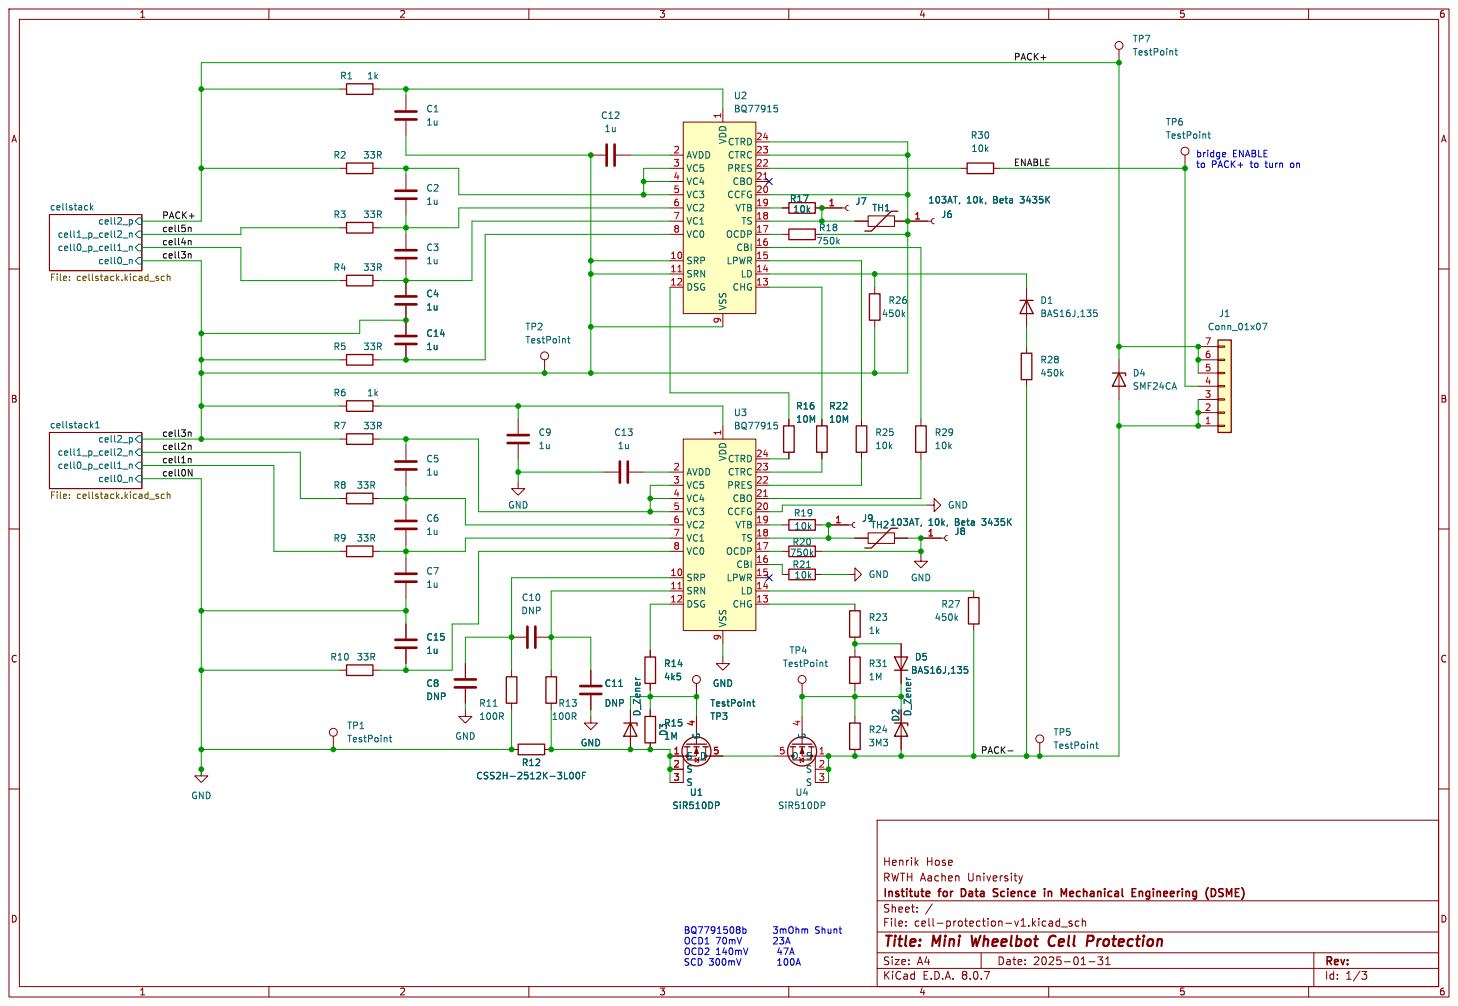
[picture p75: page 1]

bridge ENABLE
to PACK+ to turn on

File: cell-protection-v1.kicad_sch Sheet: /
Id: 1/3 Title: Mini Wheelbot Cell Protection

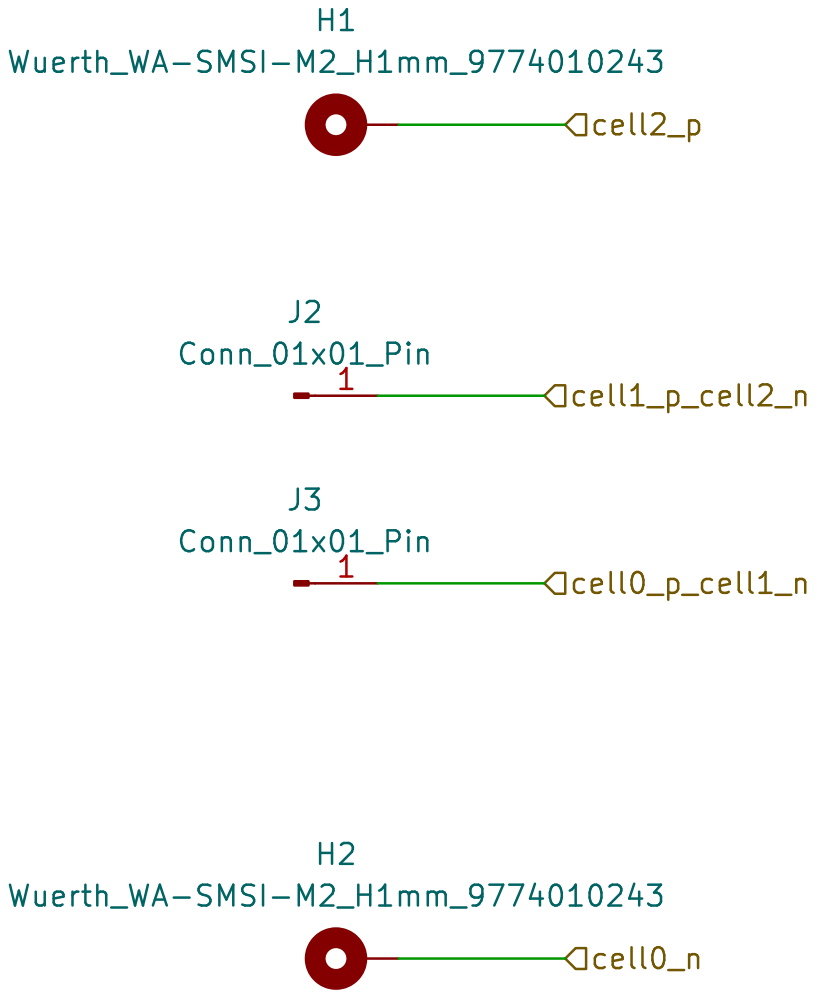
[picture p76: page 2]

File: cellstack.kicad_sch Sheet: /cellstack/
Id: 2/3 Title: Mini Wheelbot Cell Protection


File: cellstack.kicad_sch Sheet: /cellstack1/
Id: 3/3 Title: Mini Wheelbot Cell Protection

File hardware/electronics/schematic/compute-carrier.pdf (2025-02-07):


4 SDA 5 SCL 6 WP 7 VCC

Id: 1/3 Title: Mini Wheelbot Compute Carrier File: computecarrier-v1.kicad_sch Sheet: /


600mA Max 600mA Max NB SD signals are only available

Id: 2/3 Title: Mini Wheelbot Compute Carrier File: cm4.kicad_sch Sheet: /cm4/


Id: 4/3 Title: Mini Wheelbot Compute Carrier File: can.kicad_sch Sheet: /can/

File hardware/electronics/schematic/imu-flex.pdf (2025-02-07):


3 3 | 10 10
4 4 | 9 9
5 5 | 8 8

File: imu-flex-1-v1.kicad_sch Sheet: /
Id: 1/3 Title: Mini Wheelbot IMU Flex


2 ON/~{OFF} 3 ADJ 4 VOUT 5 U1

6 PS 7 SCx 8 SDx 9 U2BMI088 GND

File: imu.kicad_sch Sheet: /imu/
Id: 2/3 Title: Mini Wheelbot IMU Flex


2 ON/~{OFF} 3 ADJ 4 VOUT 5 U3

6 PS 7 SCx 8 SDx 9 U4BMI088 GND GND

File: imu.kicad_sch Sheet: /imu1/
Id: 3/3 Title: Mini Wheelbot IMU Flex

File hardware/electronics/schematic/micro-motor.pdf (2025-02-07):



3 RXD 4 CANL 6 CANH 7 U201 TCAN332 GND



2 ON/~{OFF} 3 ADJ 4 VOUT 5 U1


GHB
SHC GLC GHC GLB

INA240: REF1 and REF2 pins are swappable

current sense amp decoupling

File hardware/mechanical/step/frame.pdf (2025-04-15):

Henrik Hose; Designed by; Checked by; Approved by; Date

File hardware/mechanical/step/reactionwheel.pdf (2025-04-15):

Henrik Hose; Designed by; Checked by; Approved by; Date

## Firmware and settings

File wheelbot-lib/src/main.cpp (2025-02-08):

// MIT License

// Copyright (c) 2024 Henrik Hose
//               2024 Jan Weisgerber

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
#include <unistd.h>

#include <chrono>
#include <cstdio>
#include <memory>
#include <atomic>
#include <fstream>

#include <poll.h>

#include "wheelbot/accel.hpp"
#include "wheelbot/can.hpp"
#include "wheelbot/config.hpp"
#include "wheelbot/controller.hpp"
#include "wheelbot/constants.hpp"
#include "wheelbot/datalogger.hpp"
#include "wheelbot/estimator.hpp"
#include "wheelbot/odometry.hpp"
#include "wheelbot/gyro.hpp"
#include "wheelbot/uprightdetection.hpp"
#include "wheelbot/motorestimator.hpp"
#include "wheelbot/inputserver.hpp"

#include <nlohmann/json.hpp>
#include <argparse/argparse.hpp>
#include "quill/Quill.h"


class ControllerThread : public cactus_rt::CyclicThread {

public:
    ControllerThread(
        std::shared_ptr<MotorInterfaceThread> motor,
        const std::array<std::shared_ptr<GyroThread>,4>& gyroscopes,
        const std::array<std::shared_ptr<AccelThread>,4>& accelerometer,
        std::shared_ptr<DataLoggerThread> data_logger,
        std::shared_ptr<InputServerThread> input_server,
        Config::MainConfig config
         )
        : CyclicThread("ControllerThread", MakeRealTimeThreadConfig()),
            motor_(motor),
            gyroscopes_(gyroscopes),
            accelerometer_(accelerometer),
            data_logger_(data_logger),
            input_server_(input_server),
            main_config_(config),
            controller_(config.balancing_config, config.ampc_config, config.standup_config),
            inputs_standup_rp(config.standup_config.inputs_standup_rp),
            inputs_standup_rn(config.standup_config.inputs_standup_rn),
            inputs_laydown_rp(config.standup_config.inputs_laydown_rp),
            inputs_laydown_rn(config.standup_config.inputs_laydown_rn),
            inputs_pitch_standup_rp(config.standup_config.inputs_pitch_standup_rp),
            inputs_pitch_standup_rn(config.standup_config.inputs_pitch_standup_rn),
            controller_id_sequence(config.standup_config.controller_id_sequence),
            steady_state_control_job_duration(config.standup_config.steady_state_control_job_duration),
            regular_control_loop_update_rate(config.standup_config.regular_control_loop_update_rate),
            inputs_pitch_laydown_rp(config.standup_config.inputs_pitch_laydown_rp),
            inputs_pitch_laydown_rn(config.standup_config.inputs_pitch_laydown_rn),
            inputs_flip_standup_roll_pos(config.standup_config.inputs_flip_standup_roll_pos),
            inputs_flip_standup_roll_neg(config.standup_config.inputs_flip_standup_roll_neg),
            setpoint_(Eigen::Vector<float, 10>::Zero()),
            odometry_(Estimator<>::r)
    {
        LOG_INFO_LIMIT(std::chrono::milliseconds(100), Logger(), "Estimator X1 = {}", estimator_.X1);

        // Initialize controllers with parameters from config
        roll_standup_rp = RollStandupController(inputs_standup_rp[0], inputs_standup_rp[1], inputs_standup_rp[2]);
        roll_standup_rn = RollStandupController(inputs_standup_rn[0], inputs_standup_rn[1], inputs_standup_rn[2]);
        roll_laydown_rp = RollLayDownController(inputs_laydown_rp);
        roll_laydown_rn = RollLayDownController(inputs_laydown_rn);
        pitch_standup_rp = PitchStandupController(inputs_pitch_standup_rp[0], inputs_pitch_standup_rp[1], inputs_pitch_standup_rp[2], config.standup_config);
        pitch_standup_rn = PitchStandupController(inputs_pitch_standup_rn[0], inputs_pitch_standup_rn[1], inputs_pitch_standup_rn[2], config.standup_config);
        pitch_laydown_rp = PitchLayDownController(inputs_pitch_laydown_rp[0], inputs_pitch_laydown_rp[1], inputs_pitch_laydown_rp[2], inputs_pitch_laydown_rp[3]);
        pitch_laydown_rn = PitchLayDownController(inputs_pitch_laydown_rn[0], inputs_pitch_laydown_rn[1], inputs_pitch_laydown_rn[2], inputs_pitch_laydown_rn[3]);
        flip_standup_rp = FlipStandupController(inputs_flip_standup_roll_pos[0], inputs_flip_standup_roll_pos[1], inputs_flip_standup_roll_pos[2]);
        flip_standup_rn = FlipStandupController(inputs_flip_standup_roll_neg[0], inputs_flip_standup_roll_neg[1], inputs_flip_standup_roll_neg[2]);

        // Set control job duration for ampc-controller
        ampc_controller.control_job_duration = steady_state_control_job_duration;

        // Initialize control loop update rate for regular operation
        control_loop_update_rate = regular_control_loop_update_rate;

        // Set controller sequence, activate the first controller and initialize it
        controller_supervisor.set_controller_id_sequence(controller_id_sequence);

        if (!controller_id_sequence.empty()){
            controller_supervisor.set_first_controller_active(controller_container);
            controller_container.init();
        }

    }

    int64_t GetLoopCounter() const {
        return loop_counter_;
    }

    bool Loop(int64_t ellapsed_ns) noexcept {
        if(!starting_time.has_value()){
            starting_time=cactus_rt::NowNs();
            data_.time = 0;
        }
        else{
            data_.time = cactus_rt::NowNs() - starting_time.value();
        }
        if(!last_motor_times_.has_value()){
            auto time_now = cactus_rt::NowNs();
            last_motor_times_ = std::array<long long int, 2>{time_now, time_now};
        }

        motor_->motor.send_sync();

        Eigen::Matrix<float, 3, 4> m;
        for (size_t i=0; i<4; i++){
            m(Eigen::all, i) = gyroscopes_.at(i)->gyro.get_latest_converted_measurement();
        }

        Eigen::Matrix<float, 3, 4> a;
        for (size_t i=0; i<4; i++){
            a(Eigen::all, i) = accelerometer_.at(i)->accel.get_latest_filtered_converted_measurement();
        }

        for (auto& m : motorestimators_){
            m.predict();
        }

        while(true){
            auto res = motor_->motor.try_get_motor_state();
            if (res.has_value()){
                auto& m = motorestimators_.at(res.value().motor_id-1);
                m.update(res.value().angle);
                last_motor_times_.value().at(res.value().motor_id-1) = res.value().sync_timestamp;
            }
            else{
                break;
            }
        }

        Eigen::Matrix<float, 3,2> s = Eigen::Matrix<float, 3,2>::Zero();
        for (size_t i = 0; i < 2; i++){
            auto & m = motorestimators_.at(i);
            const auto time_now = cactus_rt::NowNs();
            auto delay = (time_now-last_motor_times_.value().at(i))/1'000'000'000.0;
            if (delay > 0.02) delay = 0;
            s(0,i) = m.get_propagated_meas_angle( delay );
            s(1,i) = m.get_propagated_velocity( delay );
            s(2,i) = m.get_acceleration();
        }

        auto x = estimator_.update(m, a, s);
        auto [odom_px, odom_py, odom_vel, odom_yaw] = odometry_.update(x(0), x(6), x(7));
        const auto is_upright = ud_.detect_latched(x);
        const auto is_in_operating_range = ud_.detect_operating_range(x);
        const auto is_in_operating_range_after_flip = ud_.detect_flip_operating_range(x);

        auto BOEXPERIMENT = false;
        if(BOEXPERIMENT){
            setpoint_counter_ += is_upright;
            if (setpoint_counter_ > 5000)   setpoint_(0) = 0.5f*std::numbers::pi_v<float>;
            if (setpoint_counter_ > 10000)  setpoint_(0) = 0;
            if (setpoint_counter_ > 15000)  setpoint_(0) = -0.5f*std::numbers::pi_v<float>;
            if (setpoint_counter_ > 20000)  setpoint_(0) = 0;
            if (setpoint_counter_ > 25000)  terminate_ = true;
        }
        else{
            input_server_->tcp_server_.set_odometry_state(WheelbotOdometryState{odom_px, odom_py, odom_vel, odom_yaw});
            auto delta_setpoint = input_server_->tcp_server_.retrieve_new_command().value_or(WheelbotInputCommand{0,0});
            setpoint_(0) = setpoint_(0) + delta_setpoint.yaw_delta;
            setpoint_(6) = setpoint_(6) + delta_setpoint.drive_delta;
        }

        // Update control_loop_update_rate if necessary.
        control_loop_update_rate = controller_supervisor.update_control_loop_update_rate(controller_container);

        if (controller_container.active_controller_id == -1 || loop_counter_ % control_loop_update_rate == 0) {
            controller_supervisor.update_control_sequence(controller_container, x);
        }

        // Check whether the robot is in the right initial position for the predefined stand-up control sequence.
        if(loop_counter_ == 0){
            controller_supervisor.check_initial_position_for_predefined_control_sequence(controller_container, x);
        }


        if (loop_counter_ % control_loop_update_rate == 0)
        {
            if (controller_container.active_controller_id != 9 &&   // For flip stand-up, there is a different supervision rule.
                controller_container.active_controller_id != 10 ) {
                    controller_supervisor.update(controller_container);
            }

            auto u = controller_container.update(x, setpoint_);
            motor_->motor.send_motor_command(u);
            data_.tau_DR_command = u;
            std::cout << "current input:"
                    << u
                    << '\n';
        }

        data_.gyro0 = m(Eigen::all,0);
        data_.gyro1 = m(Eigen::all,1);
        data_.gyro2 = m(Eigen::all,2);
        data_.gyro3 = m(Eigen::all,3);
        data_.accel0 = a(Eigen::all,0);
        data_.accel1 = a(Eigen::all,1);
        data_.accel2 = a(Eigen::all,2);
        data_.accel3 = a(Eigen::all,3);
        data_.q_yrp = x({0,1,2});
        data_.dq_yrp = x({3,4,5});
        data_.q_DR = s(0, Eigen::all);
        data_.dq_DR = s(1, Eigen::all);
        data_.ddq_DR = s(2, Eigen::all);
        data_.setpoint_yrp = setpoint_.head<3>();
        data_logger_->data_logger_.emplace_data(data_);

        loop_counter_++;

        // Catching the robot after the regular roll or pitch standup maneuvers
        if (is_in_operating_range && (
            controller_container.active_controller_id == 0 ||   // standup_roll_pos
            controller_container.active_controller_id == 1 ||   // standup_roll_neg
            controller_container.active_controller_id == 5 ||   // standup_pitch_pos
            controller_container.active_controller_id == 6 )    // standup_pitch_neg
            ) {
            std::cout << "The robot is in a position where the lqr can take over!"
                 << '\n';
            controller_supervisor.set_next_controller_active(controller_container);
        }

        // Catching the robot after the flip standup maneuvers
        if (controller_container.active_controller_id == 9 ||      // standup_flip_roll_pos
            controller_container.active_controller_id == 10 ) {    // standup_flip_pitch_neg

            if (is_in_operating_range_after_flip && controller_container.AmIDone()) {
                std::cout << "After the (hopefully) successful flip stand-up the robot is in a position where the lqr can take over!"
                    << '\n';
                controller_supervisor.set_next_controller_active(controller_container);
            }
        }

        // Crash detection

        if (controller_container.active_controller_id == 4) {
            if ((std::abs(x(1)) > 52 * M_PI / 180.0) || (std::abs(x(2)) > 56 * M_PI / 180.0)) {
                crash_detected = true;
                crash_counter_for_gentle_shutdown++;
                // After the detection of a crash, wait 4 seconds without motor input for the wheels to spin down.
                if (crash_counter_for_gentle_shutdown >= 0) {
                    LOG_INFO_LIMIT(std::chrono::milliseconds(100), Logger(), "Crash detected! \n ----------------------- \n The process crashed! \n All threads are stopped, the experiment ends with a detected crash. \n -----------------------");
                    pthread_kill(pthread_self(), SIGINT);
                }
            }
        }

        return false;
    }

private:
    std::shared_ptr<MotorInterfaceThread> motor_;
    std::array<std::shared_ptr<GyroThread>,4> gyroscopes_;
    std::array<std::shared_ptr<AccelThread>,4> accelerometer_;
    std::shared_ptr<DataLoggerThread> data_logger_;
    std::shared_ptr<InputServerThread> input_server_;
    const Config::MainConfig main_config_;
    size_t                      max_loop_counter_;
    size_t                      setpoint_counter_{0};
    size_t                      loop_counter_{0};

    static cactus_rt::CyclicThreadConfig MakeRealTimeThreadConfig() {
        cactus_rt::CyclicThreadConfig config;
        config.period_ns = 1'000'000;
        config.cpu_affinity = std::vector<size_t>{3};
        config.SetFifoScheduler(99);

        return config;
    }

    Estimator<> estimator_;
    Odometry odometry_;
    std::array<MotorEstimator, 2> motorestimators_;
    std::optional<std::array<long long int, 2>> last_motor_times_;
    ParameterAdaptiveAMPC controller_;
    Eigen::Vector<float, 10> setpoint_;
    MotorInterface<> motor_interface_;
    WheelbotStateData::Data data_;
    std::optional<uint64_t>   starting_time;

    UprightDetector ud_ = UprightDetector(main_config_.standup_config);

    bool terminate_ = false;

public:

    // Initialize all controllers with arbitrary values
    RollStandupController roll_standup_rp = RollStandupController(0,0,0);
    RollStandupController roll_standup_rn = RollStandupController(0,0,0);
    RollLayDownController roll_laydown_rp = RollLayDownController(1.0);
    RollLayDownController roll_laydown_rn = RollLayDownController(1.0);
    ParameterAdaptiveAMPC ampc_controller_ = ParameterAdaptiveAMPC(main_config_.balancing_config, main_config_.ampc_config, main_config_.standup_config);
    PitchStandupController pitch_standup_rp = PitchStandupController(0,0,0,main_config_.standup_config);
    PitchStandupController pitch_standup_rn = PitchStandupController(0,0,0,main_config_.standup_config);
    PitchLayDownController pitch_laydown_rp = PitchLayDownController(0,0,0,0);
    PitchLayDownController pitch_laydown_rn = PitchLayDownController(0,0,0,0);
    FlipStandupController flip_standup_rp = FlipStandupController(0,0,0);
    FlipStandupController flip_standup_rn = FlipStandupController(0,0,0);

    // Set pointers to controller objects
    RollStandupController& standup_roll_positive = roll_standup_rp;
    RollStandupController& standup_roll_negative = roll_standup_rn;
    ParameterAdaptiveAMPC& ampc_controller = ampc_controller_;
    RollLayDownController& laydown_roll_pos = roll_laydown_rp;
    RollLayDownController& laydown_roll_neg = roll_laydown_rn;
    PitchStandupController& standup_pitch_positive = pitch_standup_rp;
    PitchStandupController& standup_pitch_negative = pitch_standup_rn;
    PitchLayDownController& laydown_pitch_pos = pitch_laydown_rp;
    PitchLayDownController& laydown_pitch_neg = pitch_laydown_rn;
    FlipStandupController& flip_standup_roll_positive = flip_standup_rp;
    FlipStandupController& flip_standup_roll_negative = flip_standup_rn;

    // Initialize controller supervisor
    ControllerSupervisor controller_supervisor = ControllerSupervisor(main_config_.standup_config);

    // Initialize controller container
    Controller_Container controller_container =
        Controller_Container(
            standup_roll_positive, standup_roll_negative,
            laydown_roll_pos, laydown_roll_neg,
            ampc_controller,
            standup_pitch_positive, standup_pitch_negative,
            laydown_pitch_pos, laydown_pitch_neg,
            flip_standup_roll_positive, flip_standup_roll_negative);

    // Define config parameters to fill with data from config
    std::array<float, 3> inputs_standup_rp, inputs_standup_rn,
            inputs_pitch_standup_rp, inputs_pitch_standup_rn,
            inputs_flip_standup_roll_pos, inputs_flip_standup_roll_neg;

    std::array<float, 4> inputs_pitch_laydown_rp, inputs_pitch_laydown_rn;

    std::vector<int> controller_id_sequence;
    float inputs_laydown_rp, inputs_laydown_rn;
    int steady_state_control_job_duration;

    int64_t control_loop_update_rate, regular_control_loop_update_rate;

    bool crash_detected = false;
    int crash_counter_for_gentle_shutdown = 0;

};


int main(int argc, char * argv[])
{
    argparse::ArgumentParser program("Main");
    program.add_argument("-c", "--config")
        .help("path to main configuration yaml file");
    program.add_argument("-o", "--output")
        .help("path to output log csv file");

    try {
        program.parse_args(argc, argv);
    } catch (const std::exception &err) {
        std::cerr << err.what() << std::endl;
        std::cerr << program;
        return 1;
    }

    cactus_rt::App app;
    auto logger = quill::get_logger();
    LOG_INFO(logger, "Welcome to Wheelbot control app");

    #ifdef HARDWARE_BUILD
    std::string configfile = "/wheelbot-lib/config/default.json";
    #else
    std::string configfile = "../config/default.json";
    #endif
    if (program.is_used("-c")) {
        configfile = program.get("-c");
        LOG_INFO(logger, "Using user provided configfile {}", configfile);
    }
    else {
        LOG_INFO(logger, "Using default configfile {}", configfile);
    }

    std::ifstream main_config_file(configfile);
    nlohmann::json main_config_data = nlohmann::json::parse(main_config_file);
    auto main_config = main_config_data.get<Config::MainConfig>();

    #ifdef HARDWARE_BUILD
    auto loggingfile = create_filename_with_date("/wheelbot-lib/log");
    #else
    auto loggingfile = create_filename_with_date("../log");
    #endif
    if (program.is_used("-o")) {
        loggingfile = program.get("-o");
        LOG_INFO(logger, "Using user provided logfile {}", loggingfile);
    }
    else{
        LOG_INFO(logger, "Using default logfile {}", loggingfile);
    }

    auto logger_thread = std::make_shared<DataLoggerThread>(loggingfile);
    auto input_thread = std::make_shared<InputServerThread>();
    std::array gyro_threads {
        std::make_shared<GyroThread>("gyro0", R01),
        std::make_shared<GyroThread>("gyro1", R01),
        std::make_shared<GyroThread>("gyro2", R23),
        std::make_shared<GyroThread>("gyro3", R23)
        };

    std::array acc_threads {
        std::make_shared<AccelThread>("acc0", R01),
        std::make_shared<AccelThread>("acc1", R01),
        std::make_shared<AccelThread>("acc2", R23),
        std::make_shared<AccelThread>("acc3", R23)
        };

    auto motor_thread = std::make_shared<MotorInterfaceThread>("motor");
    auto controller_thread = std::make_shared<ControllerThread>(
        motor_thread, gyro_threads, acc_threads, logger_thread, input_thread, main_config);

    app.RegisterThread(motor_thread);
    for ( const auto& t : gyro_threads ){
        app.RegisterThread(t);
    }
    for ( const auto& t : acc_threads ){
        app.RegisterThread(t);
    }
    app.RegisterThread(logger_thread);
    app.RegisterThread(input_thread);
    app.RegisterThread(controller_thread);

    cactus_rt::SetUpTerminationSignalHandler();
    LOG_INFO(logger,"Testing RT loop until CTRL+C\n.");

    app.Start();

    // This function blocks until SIGINT or SIGTERM are received.
    cactus_rt::WaitForAndHandleTerminationSignal();

    app.RequestStop();
    app.Join();

    LOG_INFO(logger, "CONTROL Number of loops executed: {}", controller_thread->GetLoopCounter());
    LOG_INFO(logger, "GYRO Number of loops executed:    {}, {}, {}, {}",
        gyro_threads.at(0)->GetLoopCounter(),
        gyro_threads.at(1)->GetLoopCounter(),
        gyro_threads.at(2)->GetLoopCounter(),
        gyro_threads.at(3)->GetLoopCounter());
    LOG_INFO(logger, "ACCEL Number of loops executed:   {}, {}, {}, {}",
        acc_threads.at(0)->GetLoopCounter(),
        acc_threads.at(1)->GetLoopCounter(),
        acc_threads.at(2)->GetLoopCounter(),
        acc_threads.at(3)->GetLoopCounter());

    return 0;

}

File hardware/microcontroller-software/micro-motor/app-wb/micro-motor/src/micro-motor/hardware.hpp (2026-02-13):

/*
 * Copyright (C) 2019 Raphael Lehmann <raphael@rleh.de>
 * Copyright (C) 2021 Christopher Durand
 *
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
 * You should have received a copy of the GNU General Public License
 * along with this program.  If not, see <http://www.gnu.org/licenses/>.
 */

#ifndef HARDWARE_V2_HPP
#define HARDWARE_V2_HPP

#include <modm/platform.hpp>
#include <modm/architecture/interface/clock.hpp>
#include <modm/platform/uart/uart_1.hpp>
#include <modm/math/filter/moving_average.hpp>

#include <librobots2/motor/motor_bridge.hpp>


using namespace modm::platform;

namespace Board
{
	using namespace modm::literals;

/// STM32G474RE running at 170MHz generated from the internal 16MHz crystal
// Dummy clock for devices
struct SystemClock {
	static constexpr uint32_t Frequency = 170_MHz;
	static constexpr uint32_t Ahb1      = Frequency;
	static constexpr uint32_t Ahb2      = Frequency;
	static constexpr uint32_t Apb1      = Frequency;
	static constexpr uint32_t Apb2      = Frequency;

	static constexpr uint32_t Cordic    = Ahb1;
	static constexpr uint32_t Crc       = Ahb1;
	static constexpr uint32_t Dma       = Ahb1;
	static constexpr uint32_t Dma1      = Dma;
	static constexpr uint32_t Dma2      = Dma;
	static constexpr uint32_t DmaMux    = Dma;
	static constexpr uint32_t Fmac      = Ahb1;

	static constexpr uint32_t Adc       = Ahb2;
	static constexpr uint32_t Adc1      = Adc;
	static constexpr uint32_t Adc2      = Adc;
	static constexpr uint32_t Adc3      = Adc;
	static constexpr uint32_t Adc4      = Adc;
	static constexpr uint32_t Adc5      = Adc;
	static constexpr uint32_t Dac       = Ahb2;
	static constexpr uint32_t Dac1      = Dac;
	static constexpr uint32_t Dac2      = Dac;
	static constexpr uint32_t Dac3      = Dac;
	static constexpr uint32_t Dac4      = Dac;
	static constexpr uint32_t Rng       = Ahb2;

	static constexpr uint32_t Can       = Apb1;
	static constexpr uint32_t Fdcan1    = Can;
	static constexpr uint32_t Fdcan2    = Can;
	static constexpr uint32_t Fdcan3    = Can;
	static constexpr uint32_t I2c       = Apb1;
	static constexpr uint32_t I2c1      = I2c;
	static constexpr uint32_t I2c2      = I2c;
	static constexpr uint32_t I2c3      = I2c;
	static constexpr uint32_t I2c4      = I2c;
	static constexpr uint32_t Lptim     = Apb1;
	static constexpr uint32_t Lpuart    = Apb1;
	static constexpr uint32_t Rtc       = Apb1;
	static constexpr uint32_t Spi2      = Apb1;
	static constexpr uint32_t Spi3      = Apb1;
	static constexpr uint32_t Uart4     = Apb1;
	static constexpr uint32_t Uart5     = Apb1;
	static constexpr uint32_t Usart2    = Apb1;
	static constexpr uint32_t Usart3    = Apb1;
	static constexpr uint32_t Usb       = Apb1;
	static constexpr uint32_t Apb1Timer = Apb1 * 1;
	static constexpr uint32_t Timer2    = Apb1Timer;
	static constexpr uint32_t Timer3    = Apb1Timer;
	static constexpr uint32_t Timer4    = Apb1Timer;
	static constexpr uint32_t Timer5    = Apb1Timer;
	static constexpr uint32_t Timer6    = Apb1Timer;
	static constexpr uint32_t Timer7    = Apb1Timer;

	static constexpr uint32_t Sai1      = Apb2;
	static constexpr uint32_t Spi1      = Apb2;
	static constexpr uint32_t Usart1    = Apb2;
	static constexpr uint32_t Apb2Timer = Apb2 * 1;
	static constexpr uint32_t Timer1    = Apb2Timer;
	static constexpr uint32_t Timer8    = Apb2Timer;
	static constexpr uint32_t Timer15   = Apb2Timer;
	static constexpr uint32_t Timer16   = Apb2Timer;
	static constexpr uint32_t Timer17   = Apb2Timer;
	static constexpr uint32_t Timer20   = Apb2Timer;

	static bool inline
	enable()
	{
		Rcc::enableInternalClock();	// 16MHz
		Rcc::PllFactors pllFactors{
			.pllM = 4,	//  16MHz / M= 4 ->   4MHz
			.pllN = 85,	//   4MHz * N=85 -> 340MHz
			.pllR = 2,	// 336MHz / R= 2 -> 170MHz = F_cpu
		};
		Rcc::enablePll(Rcc::PllSource::InternalClock, pllFactors);
		// set flash latency for 170MHz
		Rcc::setFlashLatency<Frequency>();
		// switch system clock to PLL output
		Rcc::enableSystemClock(Rcc::SystemClockSource::Pll);
		Rcc::setAhbPrescaler(Rcc::AhbPrescaler::Div1);
		// APB1 has max. 170MHz
		Rcc::setApb1Prescaler(Rcc::Apb1Prescaler::Div1);
		Rcc::setApb2Prescaler(Rcc::Apb2Prescaler::Div1);
		// update frequencies for busy-wait delay functions
		Rcc::updateCoreFrequency<Frequency>();

		Rcc::setCanClockSource(Rcc::CanClockSource::Pclk);

		return true;
	}
};
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

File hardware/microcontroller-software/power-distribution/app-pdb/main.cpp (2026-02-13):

// #include <modm/platform.hpp>
// #include <modm/debug/logger.hpp>
// #include <modm/processing/fiber/scheduler.hpp>
// #include <modm/processing/fiber.hpp>
#include "modm/platform.hpp"
#include "modm/debug/logger.hpp"
#include "modm/processing/fiber/scheduler.hpp"
#include "modm/processing/fiber.hpp"
#include "board.hpp"
#include "data.hpp"
#include "tasks/can_thread.hpp"
#include "tasks/control_thread.hpp"
#include "tasks/pdb_thread.hpp"
#include "tasks/debug_thread.hpp"
#include "tasks/buzzer_thread.hpp"

#include <modm/math/filter/pid.hpp>

using namespace Board;
using namespace modm::literals;


// modm::IODeviceWrapper< Board::Ui::DebugUart, modm::IOBuffer::BlockIfFull > loggerDevice;
modm::log::Logger modm::log::debug(loggerDevice);
modm::log::Logger modm::log::info(loggerDevice);
modm::log::Logger modm::log::warning(loggerDevice);
modm::log::Logger modm::log::error(loggerDevice);

using PidParameters = modm::Pid<float>::Parameter;
using Pid = modm::Pid<float>;
// auto braking_pid_parameters = PidParameters{0.005, 0.005, 0, 0.9/0.01, 0.9};
auto braking_pid_parameters = PidParameters{0.2, 0.001, 0, 0.9/0.01, 1};
auto braking_pid = Pid{braking_pid_parameters};

constexpr auto i_drive_max = 15.f; // [A]
constexpr auto v_supply_min = 15.f; // [V]

float braking_pid_value{0};

bool break_overwrite{0};

std::atomic<float> last_motor_current;

MODM_ISR(TIM8_UP)
{
	using Timer = Board::DrivePower::BrakingTimer;
	Timer::acknowledgeInterruptFlags(Timer::InterruptFlag::Update);

	float v_supply = Adc1::getValue() * DrivePower::v_supply_div;
	float i_drive  = static_cast<float>(
		static_cast<int>(Adc2::getValue()) - 0x7ff)* DrivePower::i_drive_div;
	last_motor_current.store(i_drive, std::memory_order_relaxed);
	// if (i_drive >= i_drive_max){
	// 	// trigger estop!!!
	// 	DrivePower::disableDrive();
	// 	LogicPower::EnableMotor1::reset();
	// 	LogicPower::EnableMotor2::reset();
	// }

	if (v_supply <= v_supply_min){
		// trigger estop!!!
		DrivePower::disableDrive();
		LogicPower::EnableMotor1::reset();
		LogicPower::EnableMotor2::reset();
		MODM_LOG_INFO.printf("V_supply < V_supply_min\n");
	}

	braking_pid.update(v_supply-DrivePower::v_supply_max);
	braking_pid_value = braking_pid.getValue();

	if(break_overwrite){
		DrivePower::setBrakingCompareValue(DrivePower::MaxPwm);
	}
	else if ( braking_pid_value > 0 ) {
		uint16_t output = braking_pid_value*DrivePower::MaxPwm;
		DrivePower::setBrakingCompareValue(output);
	}
	else {
		DrivePower::setBrakingCompareValue(0);
	}

}

CanThread can_thread(main_configuration, can_thread.safety_timeout);
ControlThread control_thread(main_configuration);
PDBThread pdb_thread(main_configuration);
DebugThread debug_thread(main_configuration);
BuzzerThread buzzer_thread(main_configuration);


extern modm::Fiber<2048> fiber_can_thread_run;

modm_faststack modm::Fiber<2048> fiber_can_thread_run([](){
	can_thread.initialize();
	while(1){
		can_thread.run();
		modm::this_fiber::yield();
	}
	}, modm::fiber::Start::Later);


modm_faststack modm::Fiber<2048> fiber_control_thread_run([](){
	while(1){
		control_thread.run();
		modm::this_fiber::yield();
	}
}, modm::fiber::Start::Later);

modm_faststack modm::Fiber<2048> fiber_pdb_thread_run([](){
	pdb_thread.initialize();
	while(1){
		pdb_thread.run();
		modm::this_fiber::yield();
	}
}, modm::fiber::Start::Later);

modm_faststack modm::Fiber<2048> fiber_debug_thread_run([](){
	while(1){
		debug_thread.run();
		float i_drive  = last_motor_current.load(std::memory_order_relaxed);
		MODM_LOG_INFO << "Measured drive current: " << int{i_drive*1000} << " mA" << modm::endl;
		modm::this_fiber::sleep_for(100ms);
		modm::this_fiber::yield();
	}
}, modm::fiber::Start::Later);

modm_faststack modm::Fiber<2048> fiber_buzzer_thread_run([](){
	while(1){
		buzzer_thread.run();
		modm::this_fiber::yield();
	}
	}, modm::fiber::Start::Later);

class UiBuzzer{
public:
	modm::ShortTimeout timeout;
	enum class State{
		On, Off
	};

	State state{State::Off};

public:
	void
	update(){
		if(timeout.execute() && (state==State::On)){
			Ui::buzzerOff();
			state=State::Off;
		}
	}

	template< typename Rep, typename Period >
	void
	beep(std::chrono::duration<Rep, Period> interval){
		Ui::buzzerOn();
		state=State::On;
		timeout.restart(interval);
	}

};



class EStop{
public:
	enum struct State{
		Stop = 0,
		Arm = 1,
		Running = 2
	};

	modm::ShortPeriodicTimer timeout;
	State current_state{State::Arm};

	UiBuzzer buzzer;

	template< typename Rep, typename Period >
	EStop(std::chrono::duration<Rep, Period> interval)
		: timeout(modm::ShortPeriodicTimer{interval})
	{};

	void executeStop(){
		current_state = State::Stop;
		DrivePower::disableDrive();
		LogicPower::EnableMotor1::reset();
		LogicPower::EnableMotor2::reset();
	}

	void executeArmToRunning(){
		current_state = State::Running;
		DrivePower::enableDrive();
		LogicPower::EnableMotor1::set();
		LogicPower::EnableMotor2::set();
		buzzer.beep(500ms);
	}

	void executeStopToArm(){
		current_state = State::Arm;
	}

	void update(){
		buzzer.update();
		if (timeout.execute()){
			if (current_state==State::Running || current_state == State::Arm){
				executeStop();
			}
			DrivePower::disableDrive();
		}
		if (Nrf::Data::Packet packet; Nrf::Data::getPacket(packet))
		{
			if (static_cast<State>(packet.payload[0]) == State::Stop){
				executeStop();
			}
			else if (current_state == State::Arm && static_cast<State>(packet.payload[0]) == State::Running){
				executeArmToRunning();
			}
			else if( ( current_state == State::Stop ) && static_cast<State>(packet.payload[0]) == State::Arm){
				executeStopToArm();
			}

			// if (current_state != State::Stop){
			timeout.restart();
			// }

			// MODM_LOG_INFO << "Receiving packet " << packet.payload[0] << " from " << packet.getSource() << modm::endl;

		}
	}

	inline
	State getCurrentState(){
		return current_state;
	}
};

void COMP1_2_3_IRQHandler(void)
{
    // Clear pending EXTI flag
    EXTI->PR1 = (1U << 21);

	DrivePower::disableDrive();

	main_configuration.buzzer_action = Configuration::BuzzerActions::buzzingShortCircuitBreak;
}
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

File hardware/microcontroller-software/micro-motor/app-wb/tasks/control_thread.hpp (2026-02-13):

/* control_thread.hpp
*
* Copyright (C) 2024 Henrik Hose
*
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
* You should have received a copy of the GNU General Public License
* along with this program.  If not, see <http://www.gnu.org/licenses/>.
*/

#ifndef CONTROL_THREAD_HPP
#define CONTROL_THREAD_HPP

#include <modm/processing.hpp>
#include <modm/driver/motor/drv832x_spi.hpp>
#include "../data.hpp"
#include "../encoder.hpp"

constexpr
Configuration::BldcMotorParameters mn4006Parameters{
	.inductance = 80.e-6f,
	.resistance = 150.e-3f,
	.electrical_per_mechanical_rev = 12.f,
	.control_bandwidth= 5000.f,
	.cogging_correction_factor=1.2f,
	.initialized=true
};


extern modm::Fiber<16000> fiber_control_thread_calibration;
class ControlThread
{
public:
	ControlThread(Configuration &config) : config(config), safety_timeout(std::chrono::milliseconds(200)) {}

	void
	run()
	{
		if (config.special_action == Configuration::SpecialActions::EncoderCalibrationStart){
			MODM_LOG_INFO << "Entering encoder Offset Calibration" << modm::endl;
			config.foc.foc_state = Configuration::FocState::Disable;
			config.special_action = Configuration::SpecialActions::EncoderCalibrationRunning;
			run_encoder_offset_calibration();
			config.special_action = Configuration::SpecialActions::EncoderCalibrationSuccess;
		}
		else if (config.special_action == Configuration::SpecialActions::CoggingCalibrationStart){
			config.special_action = Configuration::SpecialActions::CoggingCalibrationRunning;
			fiber_control_thread_calibration.start();
		}
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

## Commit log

2025-02-08 wheelbot-lib update
2025-04-15 Draft Bill of Mateerials, manufacturing STEP files
    [actuator_rotor.obj, actuator_rotor.stl, body.stl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]
2025-05-14 added stl and stp of 3D printed components
    [battery_back.stl, battery_back.stp, battery_front.stl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]
2025-06-16 updated encoder spi schematic
2025-06-16 BoM update
2025-06-16 fixup! BoM update
2025-06-16 fixup! fixup! BoM update
2025-06-16 fixup! fixup! fixup! BoM update
2025-06-17 BoM added ntc battery
2025-06-17 added how to assemble the Mini Wheelbot
2025-06-23 correct BOM: M2x8 socket head screw and brass inserts
2025-08-26 added gerbers and restructured schematics
    [cell-adapter-v1.kicad_pcb_positions.csv, cell-protection-v1.kicad_pcb_positions.csv, computecarrier-v1.kicad_pcb_positions.csv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]
2025-09-29 updated bom with gerbers, stiffener on flex pcb, new evo motor
2025-09-29 fixup bom
2025-10-06 added dimensions for flex-pcb ordering
2025-10-13 updated flex pcb gerbers with layer User1 for stiffener
2025-10-13 fixed link in bom
2025-10-22 corrected specs for pcbs in bom
2025-10-23 updated bom with magnet holder
    [magnet_adapter.stl]
2025-10-23 fixed imu flex pcb gerbers
2025-10-28 fixed flex 1 pcb short
2025-11-05 added instructions for battery assembly
2025-11-05 added BoMs
    [cell-adapter-v1.kicad_pcb_bom.csv, cell-protection-v1.kicad_pcb_bom.csv, computecarrier-v1.kicad_pcb_bom.csv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]
2025-11-16 updated power distribution schematics
2025-11-18 added pcb front and back side images
2025-11-25 add scripts to automatically set motorControllerIDs and to calibrate motors
2025-11-25 add progress for motor calibration
2026-02-13 micro-motor software to wheelbot-production
2026-02-13 power-distribution software to production
2026-02-13 power distribution fimrware binary
2026-02-13 updated bom, motor assembly, firmware flashing
    [motor_fixture_MN4006.stl, motor_fixture_MN4006_EVO.stl, motor_removal_fixture.stl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]
2026-03-04 fixed wheelbot sim missing wheelbot_model.py
2026-03-04 fixed readme wheelbot dynamics
2026-04-01 update bom
2026-04-14 added cm4 buildroot and instructions
    [config_wheelbot_cm4_64bit.txt, genimage-wheelbot_cm4.cfg]

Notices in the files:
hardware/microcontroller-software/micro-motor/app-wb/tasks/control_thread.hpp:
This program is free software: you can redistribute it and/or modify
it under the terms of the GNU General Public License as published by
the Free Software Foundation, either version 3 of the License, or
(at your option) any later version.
